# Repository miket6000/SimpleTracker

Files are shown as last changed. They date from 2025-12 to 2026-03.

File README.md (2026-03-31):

# SimpleTracker

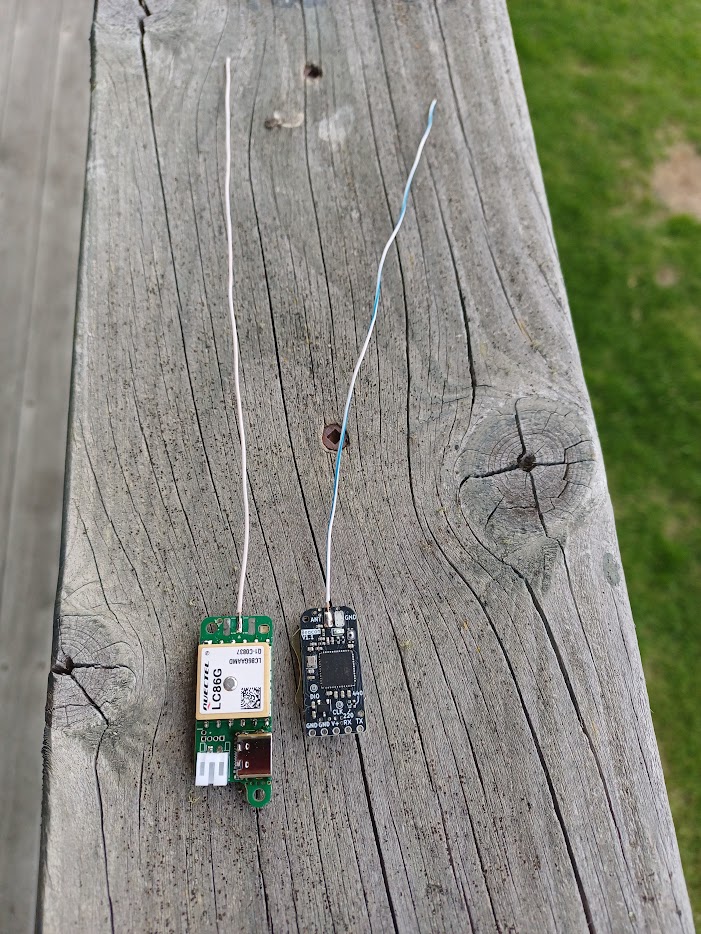
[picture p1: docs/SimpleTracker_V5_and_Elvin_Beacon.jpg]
Photo comparing SimpleTracker to an Elvin Beacon for size Comparison of SimpleTracker \(on the left\) and Elvin Beacon


SimpleTracker is a low cost and easy to use GPS tracker for model rocketry. It can operate of a single 3.7V lipo battery and has a built in charger to enable "plug-&-play" usability. The GPS coordinates of the SimpleTracker are transmitted via 433MHz LoRa every second providing several km of tracking range depending on the antenna used on the SimpleTracker and the ground station. SimpleTracker can also be used as a minimal ground station, reporting the location of a paired tracker via USB serial connection to a PC or phone.

## Hardware

The hardware is fairly minimal. It consist of a battery charger, two 3.3V linear power supplies, a LoRa radio module, GPS and a micro controller with a couple of LEDs to provide status. Bootmode can be enabled by removing the battery and shorting the 'b' and 'v' pins together on the PCB while plugging the tracker into USB. This will put the device into DFU mode so that it can be programmed using dfu-util or STM's programming utilities.

The tracker can be powered by either USB (such as when used as a ground station) or via an AltusMetrum compatible 1s lithium battery. There is an included battery charger that will charge the battery at 100mA if USB is plugged in, so it is recommended that the tracker battery be between 100mAh (to avoid charging it too fast) and 300mAh (to avoid taking too long to charge). Of course there is no upper limit on the capacity of the battery, you can always unplug it to use an external charger if the charge is too slow.

## Firmware
The firmware is "good enough". It can be flashed to the tracker by disconnecting the battery and shorting the "boot" pin to the 3V3 pin right beside it and then plugging in the USB C cable. This will put the tracker into DFU bootloader mode where it can be programmed using CubeIDE or dfu-util.

On power up the module will listen on 434MHz SF 9 BW 125kHz for a command asking for it's UID, or telling it to start transmitting on another channel. Alternatively it can recieve a command via USB if it's acting as a ground station in which case it will issue commands to other trackers. This is all orchestrated by the application.

The LED provides status information via as follows:
 - 1 flash followed by 1 flash - Tracker mode, Waiting for GPS fix
 - 1 flash followed by 2 flashes - Tracker mode, GPS fix is valid
 - 2 flashes followed by 1 flash - Ground station mode, waiting for remote tracker GNSS fix
 - 2 flashes followed by 2 flashes - Ground station mode, remote tracker has GNSS fix
 - 3 flahses - Ground station mode, no remote tracker detected on the current channel in the last 10 seconds

## Application

I decided the application deserved it's own repository, so has been moved to [https://github.com/miket6000/SimpleSuite](https://github.com/miket6000/SimpleSuite). It is built and tested in Linux, with plans on supporting Android.

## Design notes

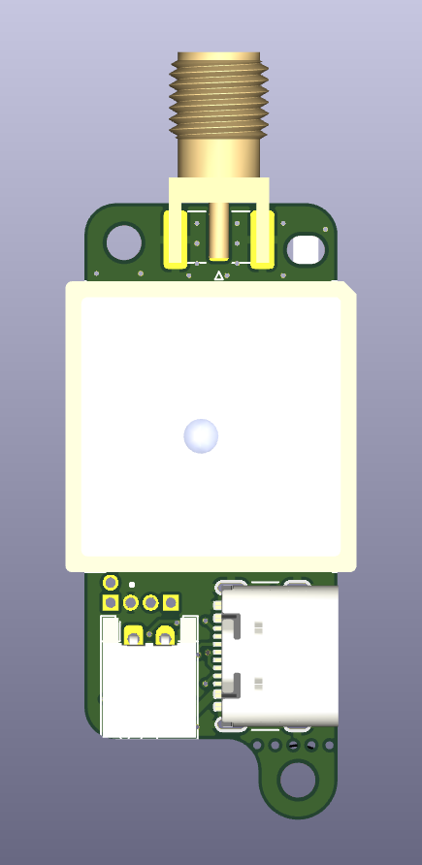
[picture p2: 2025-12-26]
docs/FrontRender.png

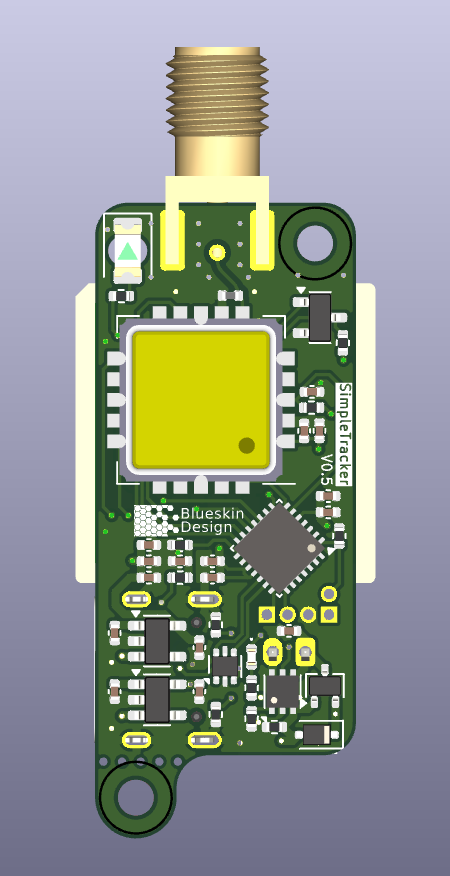
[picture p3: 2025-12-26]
docs/BackRender.png

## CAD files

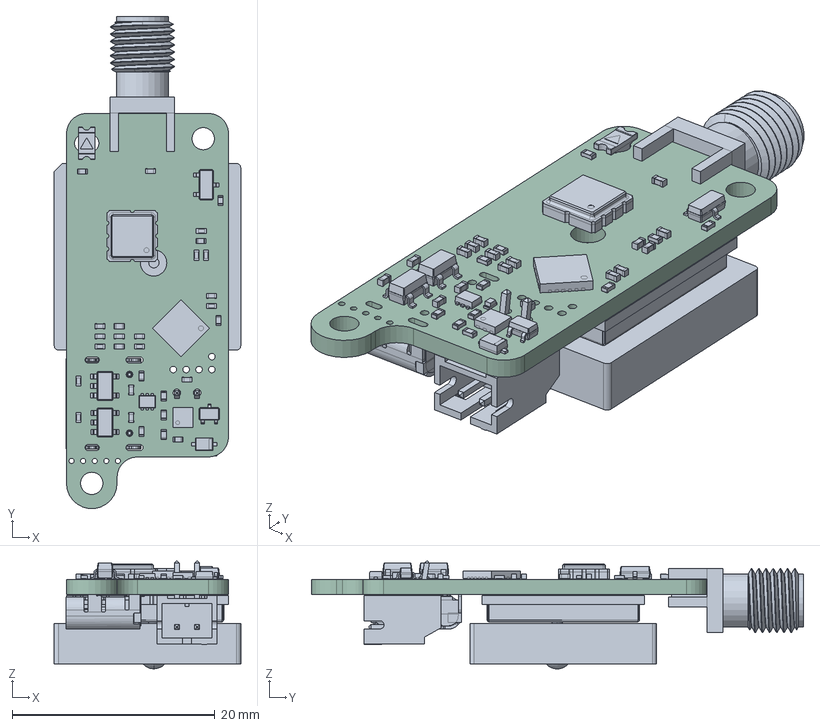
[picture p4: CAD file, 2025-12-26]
hardware/GPS Tracker.step
18.4 x 48.5 x 10.7 mm
SOT-323_SC-70
C_0402_1005Metric x 16
SOT-666
R_0402_1005Metric x 11
LED_1206_3216Metric_Castellated
L_0402_1005Metric
Analog_LCC-8_5x5mm_P1.27mm
LED_0402_1005Metric
D_SOD-323F
SOT-23
DFN-6-1EP_2x2mm_P0.65mm_EP1x1.6mm
SOT-23-5 x 2
QFN-24-1EP_4x4mm_P0.5mm_EP2.7x2.7mm
SMA_Samtec_SMA-J-P-H-ST-EM1_EdgeMount
USB_C_Receptacle_GCT_USB4105-xx-A_16P_TopMnt_Horizontal
LC86G
JST_PH_S2B-PH-K_1x02_P2.00mm_Horizontal
GPS Tracker_PCB

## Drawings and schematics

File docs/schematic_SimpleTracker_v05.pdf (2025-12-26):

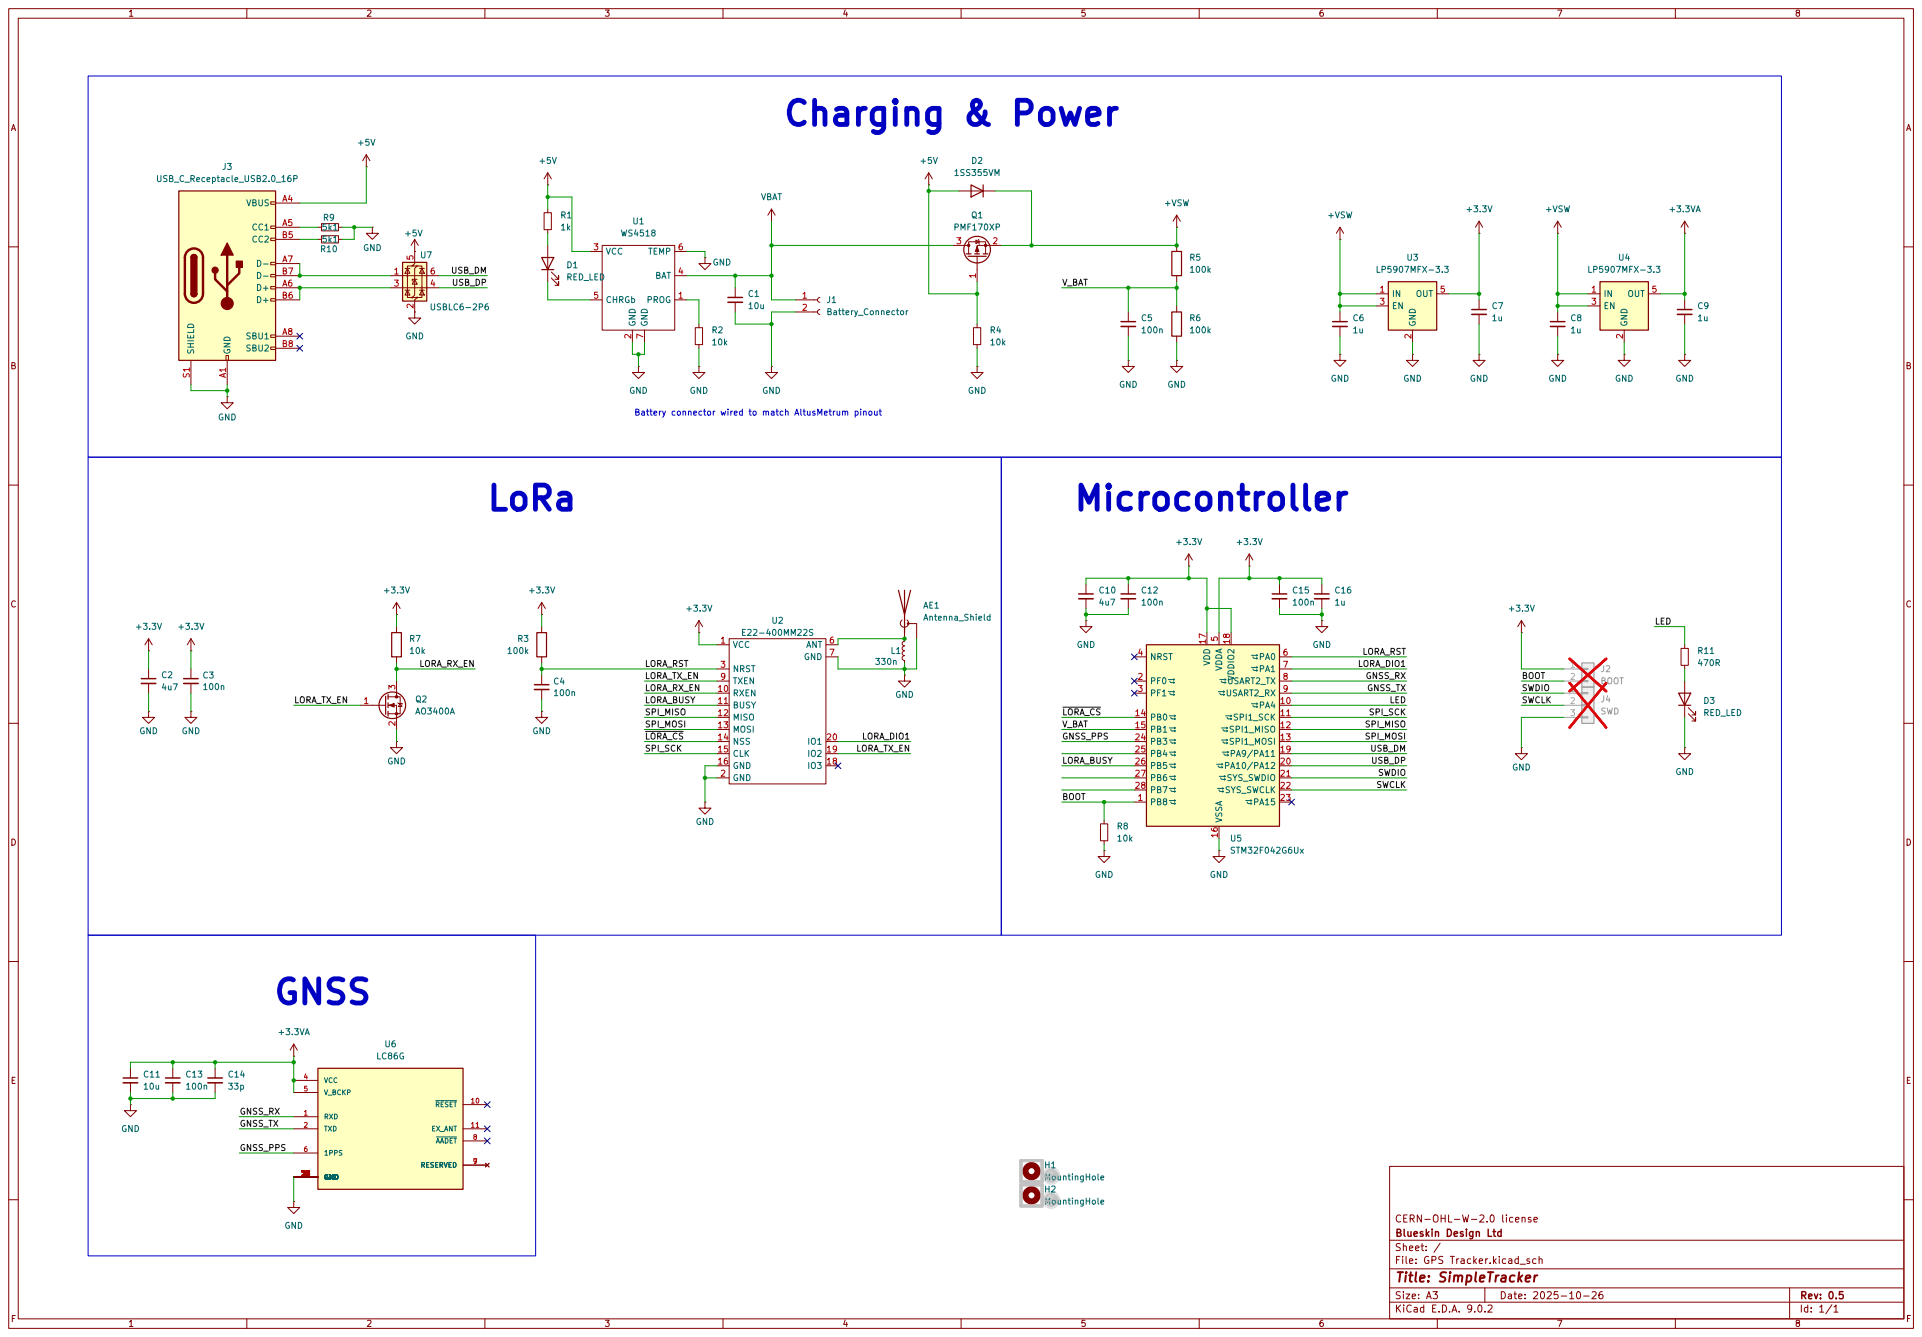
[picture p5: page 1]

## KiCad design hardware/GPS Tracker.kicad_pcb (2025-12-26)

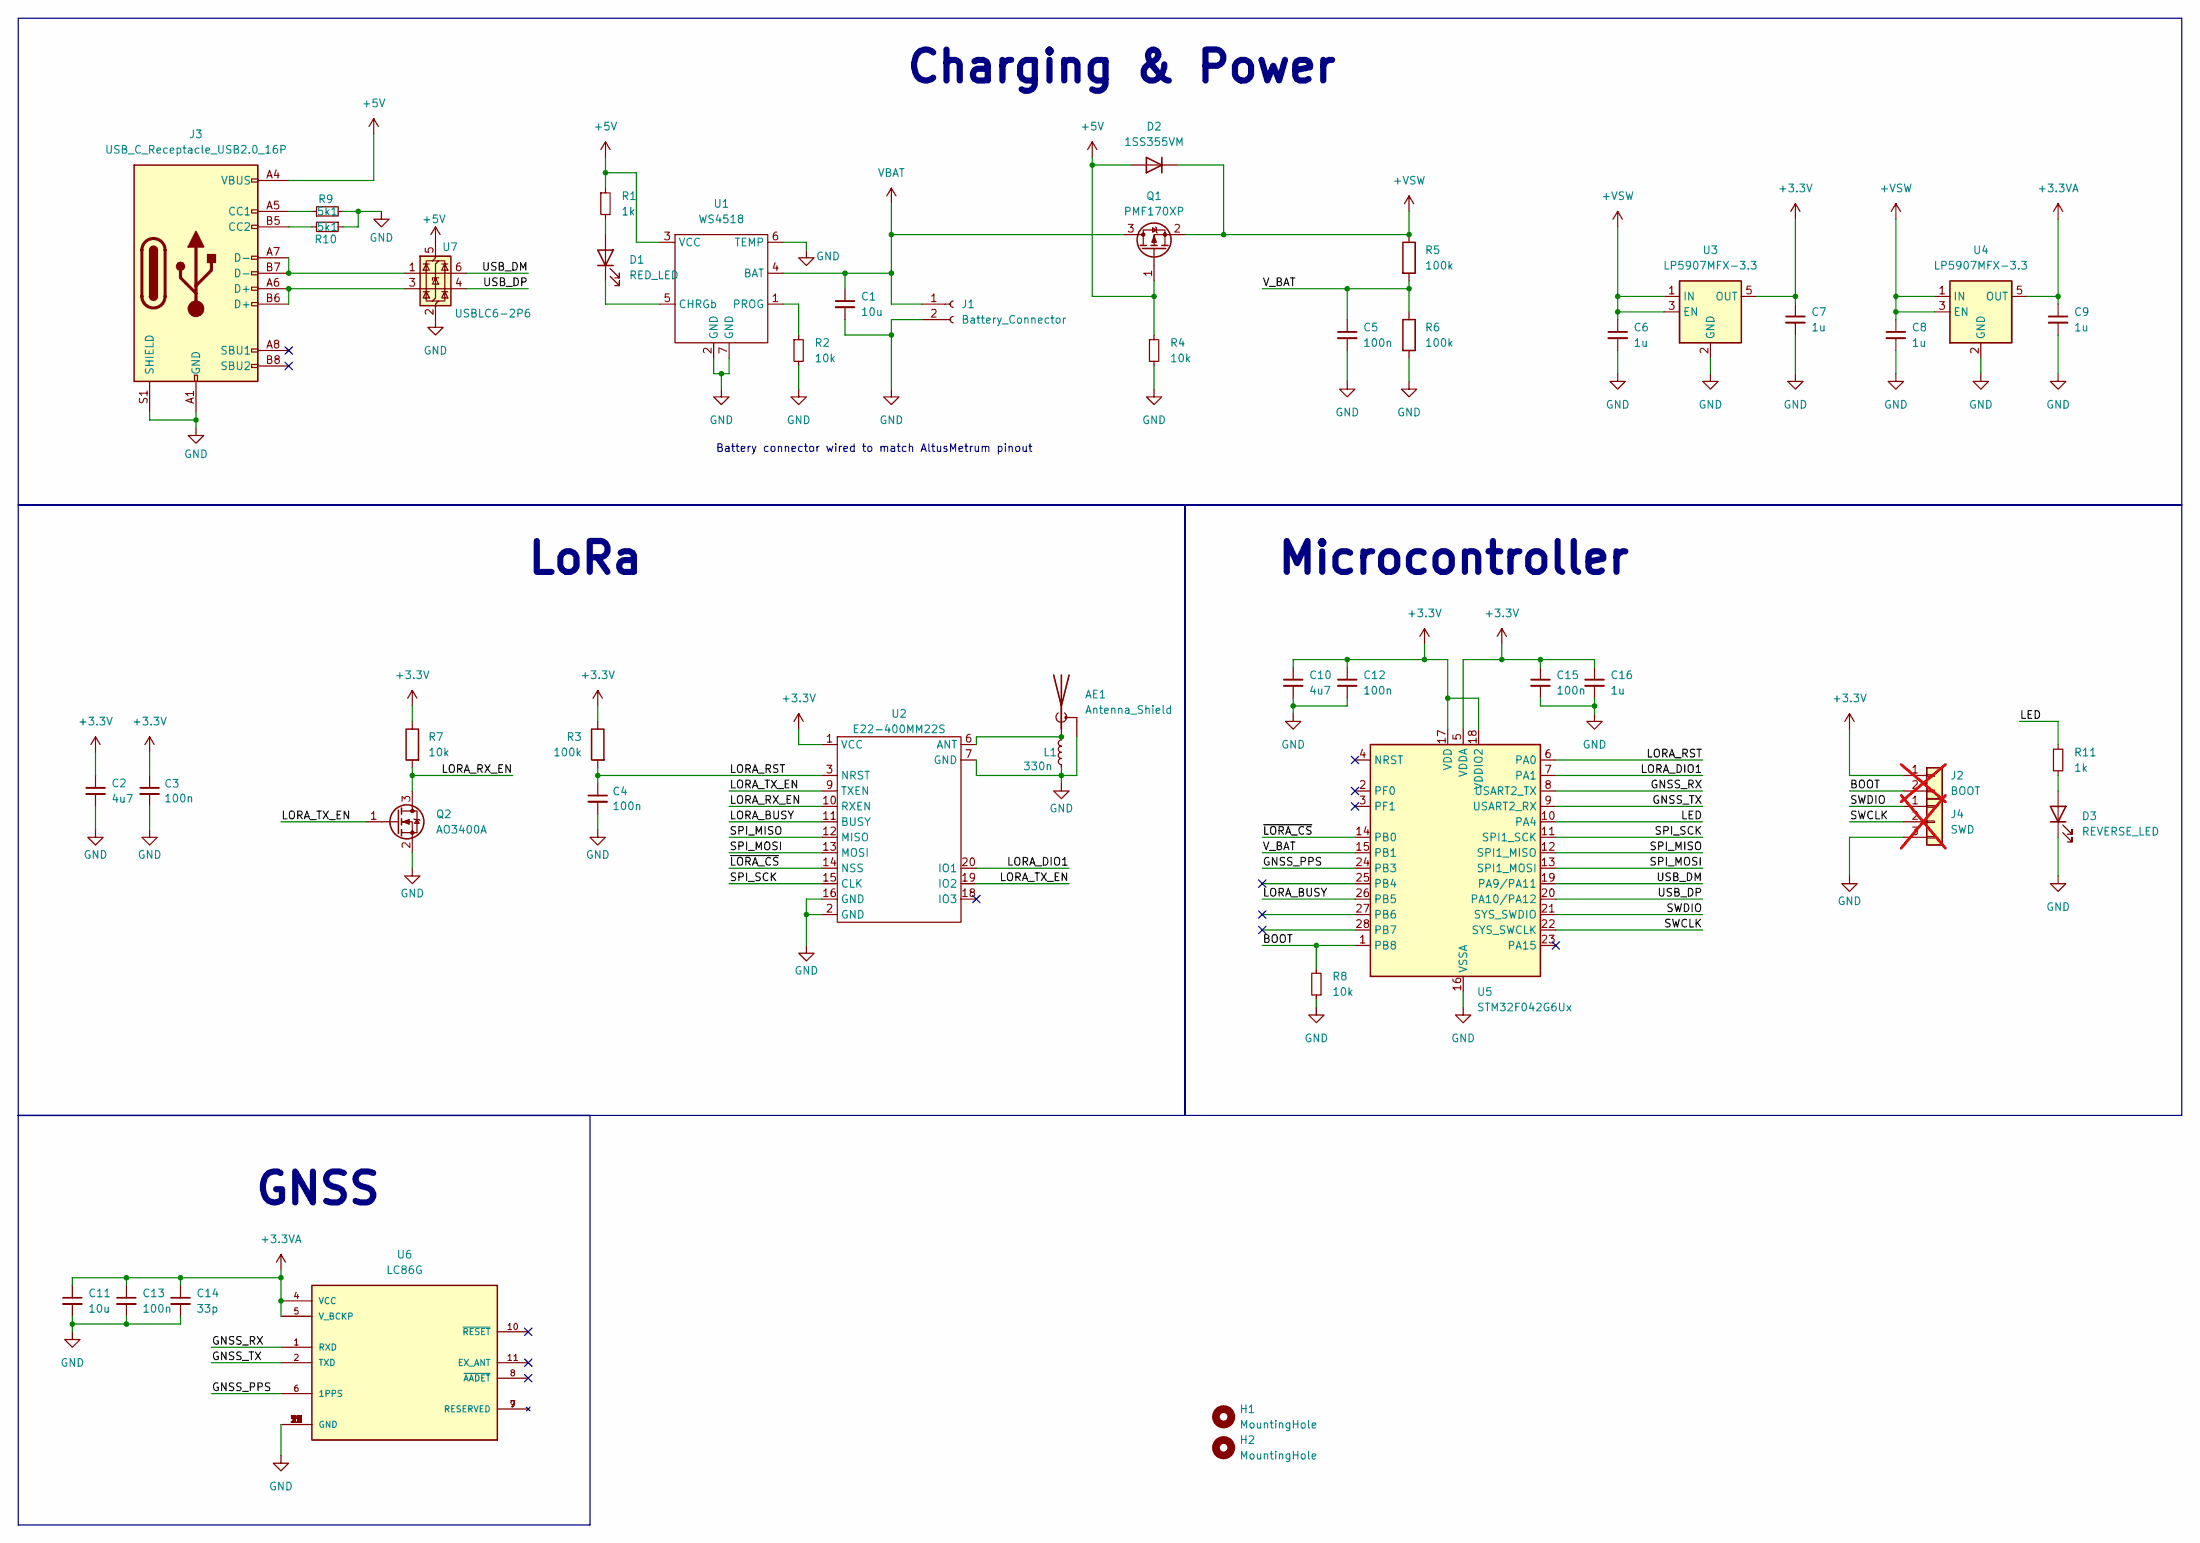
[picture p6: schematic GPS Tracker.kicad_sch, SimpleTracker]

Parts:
AE1: Antenna_Shield; SMA_EdgeMount
C1, C11: 10u; C_0402_1005Metric; JLCPCB Part # C15525
C2, C10: 4u7; C_0402_1005Metric; JLCPCB Part # C23733
C3, C4, C5, C12, C13, C15: 100n; C_0402_1005Metric; JLCPCB Part # C1525
C6, C7, C8, C9, C16: 1u; C_0402_1005Metric; JLCPCB Part # C52923
C14: 33p; C_0402_1005Metric; JLCPCB Part # C1562
D1: RED_LED; LED_0402_1005Metric
D2: 1SS355VM; D_SOD-323F
D3: REVERSE_LED; LED_1206_3216Metric_ReverseMount_Hole1.8x2.4mm; JLCPCB Part # C125107
H1, H2: MountingHole; MountingHole_2.2mm_M2
J1: Battery_Connector; JST_PH_S2B-PH-K_1x02_P2.00mm_Horizontal
J2: BOOT; PinHeader_1x02_P1.27mm_Vertical; not fitted
J3: USB_C_Receptacle_USB2.0_16P; USB_C_Receptacle_GCT_USB4105-xx-A_16P_TopMnt_Horizontal
J4: SWD; PinHeader_1x03_P1.27mm_Vertical; not fitted
L1: 330n; L_0402_1005Metric; JLCPCB Part # C89954
Q1: PMF170XP; SOT-323_SC-70
Q2: AO3400A; SOT-23; JLCPCB Part # C20917
R1, R11: 1k; R_0402_1005Metric; JLCPCB Part # C11702
R2, R4, R7, R8: 10k; R_0402_1005Metric; JLCPCB Part # C25744
R3, R5, R6: 100k; R_0402_1005Metric; JLCPCB Part # C25741
R9, R10: 5k1; R_0402_1005Metric; JLCPCB Part # C25905
U1: WS4518; DFN-6-1EP_2x2mm_P0.65mm_EP1x1.6mm
U2: E22-400MM22S; LCC-20_10x10_Pitch1.27mm
U3, U4: LP5907MFX-3.3; SOT-23-5; JLCPCB Part # C80670
U5: STM32F042G6Ux; QFN-28_4x4mm_P0.5mm
U6: LC86G; XCVR_LC86G_AA
U7: USBLC6-2P6; SOT-666

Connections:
+3.3V: C2.1, C3.1, C7.1, C10.1, C12.1, C15.1, C16.1, J2.1, R3.1, R7.1, U2.1 (VCC), U3.5 (OUT), U5.5 (VDDA), U5.17 (VDD), U5.18 (VDDIO2)
+3.3VA: C9.1, C11.1, C13.1, C14.1, U4.5 (OUT), U6.4 (VCC), U6.5 (V_BCKP)
+5V: D2.2 (A), J3.A4 (VBUS), J3.A9 (VBUS), J3.B4 (VBUS), J3.B9 (VBUS), Q1.1 (G), R1.1, R4.1, U1.3 (VCC), U7.5 (VBUS)
+VSW: C6.1, C8.1, D2.1 (K), Q1.2 (S), R5.1, U3.1 (IN), U3.3 (EN), U4.1 (IN), U4.3 (EN)
/BOOT: J2.2, R8.2, U5.1 (PB8)
/GNSS_PPS: U5.24 (PB3), U6.6 (1PPS)
/GNSS_RX: U5.8 (USART2_TX), U6.1 (RXD)
/GNSS_TX: U5.9 (USART2_RX), U6.2 (TXD)
/LED: R11.1, U5.10 (PA4)
/LORA_BUSY: U2.11 (BUSY), U5.26 (PB5)
/LORA_DIO1: U2.20 (IO1), U5.7 (PA1)
/LORA_RST: C4.1, R3.2, U2.3 (NRST), U5.6 (PA0)
/LORA_RX_EN: Q2.3 (D), R7.2, U2.10 (RXEN)
/LORA_TX_EN: Q2.1 (G), U2.9 (TXEN), U2.19 (IO2)
/SPI_MISO: U2.12 (MISO), U5.12 (SPI1_MISO)
/SPI_MOSI: U2.13 (MOSI), U5.13 (SPI1_MOSI)
/SPI_SCK: U2.15 (CLK), U5.11 (SPI1_SCK)
/SWCLK: J4.2, U5.22 (SYS_SWCLK)
/SWDIO: J4.1, U5.21 (SYS_SWDIO)
/USB_DM: U5.19 (PA9/PA11), U7.6 (I/O1)
/USB_DP: U5.20 (PA10/PA12), U7.4 (I/O2)
/V_BAT: C5.1, R5.2, R6.1, U5.15 (PB1)
/~LORA_CS: U2.14 (NSS), U5.14 (PB0)
GND: AE1.2 (Shield), C1.2, C2.2, C3.2, C4.2, C5.2, C6.2, C7.2, C8.2, C9.2, C10.2, C11.2, C12.2, C13.2, C14.2, C15.2, C16.2, D3.1 (K), J1.2, J3.A1 (GND), J3.A12 (GND), J3.B1 (GND), J3.B12 (GND), J3.S1 (SHIELD), J4.3, L1.2, Q2.2 (S), R2.2, R4.2, R6.2, R8.1, R9.2, R10.1, U1.2 (GND), U1.6 (TEMP), U1.7 (GND), U2.2 (GND), U2.7 (GND), U2.16 (GND), U3.2 (GND), U4.2 (GND), U5.16 (VSSA), U6.3 (GND), U6.12 (GND), U6.13 (GND), U6.14 (GND), U6.15 (GND), U6.16 (GND), U6.17 (GND), U6.18 (GND), U6.19 (GND), U6.20 (GND), U6.21 (GND), U6.22 (GND), U6.23 (GND), U6.24 (GND), U6.25 (GND), U6.26 (GND), U6.27 (GND), U6.28 (GND), U6.29 (GND), U6.30 (GND), U6.31 (GND), U6.32 (GND), U6.33 (GND), U6.34 (GND), U6.35 (GND), U6.36 (GND), U7.2 (GND)
unnamed: AE1.1 (A), L1.1, U2.6 (ANT)
unnamed: D1.2 (A), R1.2
unnamed: D1.1 (K), U1.5 (CHRGb)
unnamed: D3.2 (A), R11.2
unnamed: J3.A5 (CC1), R9.1
unnamed: J3.B5 (CC2), R10.2
unnamed: J3.A6 (D+), J3.B6 (D+), U7.3 (I/O2)
unnamed: J3.A7 (D-), J3.B7 (D-), U7.1 (I/O1)
unnamed: R2.1, U1.1 (PROG)
VBAT: C1.1, J1.1, Q1.3 (D), U1.4 (BAT)

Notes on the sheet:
Charging & Power
GNSS
Battery connector wired to match AltusMetrum pinout
Microcontroller
LoRa

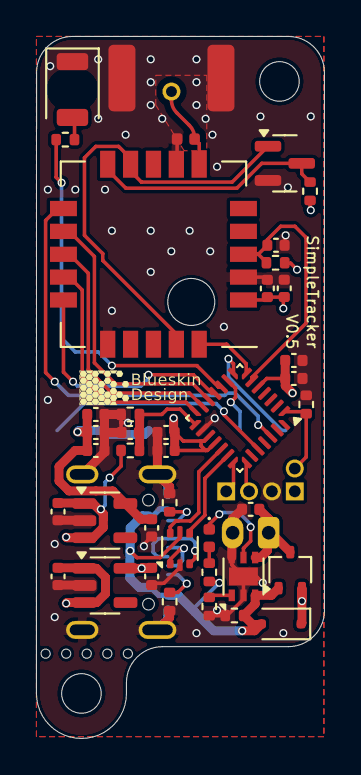
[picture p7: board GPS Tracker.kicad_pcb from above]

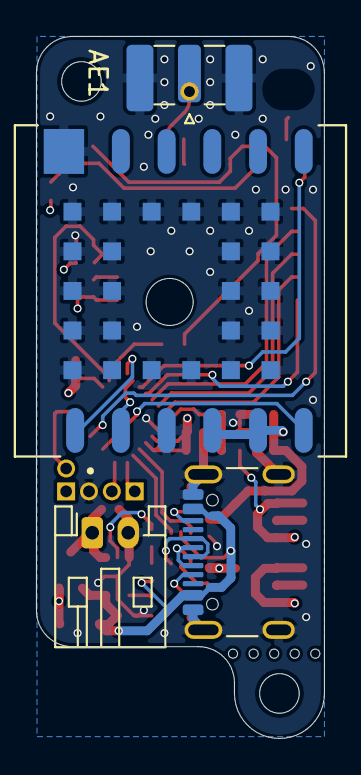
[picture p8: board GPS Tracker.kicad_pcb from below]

Board: 4 copper layers, 16.0 x 39.0 mm, 47 parts (6 on the bottom side), 34 nets.

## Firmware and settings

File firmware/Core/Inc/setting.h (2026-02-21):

#ifndef SETTING_H
#define SETTING_H
#include "main.h"
#include "lora.h"
#include "app_context.h"

#define MAX_SETTING_LIST_SIZE 10

#define DEFAULT_FREQ      434000000UL
#define DEFAULT_SF        LORA_SF9
#define DEFAULT_BW        LORA_BW_125
#define DEFAULT_CR        LORA_CR_4_5
#define DEFAULT_POWER     LORA_TX_POWER_22_DBM
#define DEFAULT_OC        150
#define DEFAULT_PREAMBLE  8
#define DEFAULT_MODE      MODE_TRACKER

typedef struct {
  char label;
  uint32_t value;
  uint32_t initial;
} Setting;

Setting **get_settings();
void setting_reset();
Setting *setting(char label);

#endif // SETTING_H

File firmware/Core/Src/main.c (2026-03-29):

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
/* Includes ------------------------------------------------------------------*/
#include "main.h"
#include "spi.h"
#include "tim.h"
#include "usart.h"
#include "gpio.h"
#include "adc.h"

/* USER CODE BEGIN Includes */
#include "clock.h"
#include "board.h"
#include "usb.h"
#include "usbd_conf.h"
#include "usbd_core.h"
#include "led.h"
#include "led_sequences.h"
#include "app_context.h"
#include "task.h"
#include "tasks.h"
#include "setting.h"
#include "filesystem.h"
#include "command.h"
#include "commands.h"
#include "gps.h"
#include "lora.h"
#include "lora_arbitration.h"
#include "lora_discovery.h"
#include "event.h"
#include "config.h"
#include <stdbool.h>
#include <stdlib.h>
#include "tusb.h"
#include "uid.h"

/* USER CODE END Includes */


/* USER CODE BEGIN PV */
LedHandle status_led;
LoRa_t hlora;

AppContext_t appContext = {
  .gpsFix = false, 
  .led = &status_led, 
  .lora = &hlora,
  .mode = MODE_GROUND_STATION,
};

/* USER CODE END PV */

/* USER CODE BEGIN 0 */

void load_settings() {
  uint8_t i = 0;
  Setting **settingList = get_settings();
  while (settingList[i] != NULL) {
    fs_read_config(settingList[i]->label, &settingList[i]->value);
    i++;
  }
}

void lora_init(LoRa_t *hlora) {
  
  hlora->frequency = setting('f')->value;
  hlora->spreadingFactor = setting('s')->value;
  hlora->bandwidth = setting('b')->value;
  hlora->codingRate = setting('c')->value;
  hlora->txPower = setting('d')->value;
  hlora->preambleLength = setting('p')->value;
  hlora->crcEnabled = 0;

  hlora->nss_port = LORA_CS_GPIO_Port;
  hlora->nss_pin = LORA_CS_Pin;
  hlora->busy_port = LORA_BUSY_GPIO_Port;
  hlora->busy_pin = LORA_BUSY_Pin;
  hlora->reset_port = LORA_RST_GPIO_Port;
  hlora->reset_pin = LORA_RST_Pin;
  hlora->dio1_port = LORA_DIO1_GPIO_Port;
  hlora->dio1_pin = LORA_DIO1_Pin;
  hlora->hspi = &hspi1;

  LoRa_Init(hlora);
}

void HAL_GPIO_EXTI_Callback(uint16_t GPIO_Pin)
{
    if (GPIO_Pin == LORA_DIO1_Pin)
    {
        LoRa_IrqHandler(appContext.lora);
    }
}

/* USER CODE END 0 */

/**
 * @brief  The application entry point.
 * @retval int
 */
int main(void) {

  /* MCU Configuration--------------------------------------------------------*/

  /* Reset of all peripherals, Initializes the Flash interface and the Systick. */
  HAL_Init();

  /* Configure the system clock */
  SystemClock_Config();

  /* Initialize all configured peripherals */
  MX_GPIO_Init();
  MX_SPI1_Init();
  MX_USB_PCD_Init();
  MX_USART2_UART_Init();
  MX_TIM16_Init();
  MX_ADC_Init();
  /* USER CODE BEGIN 2 */

  //led(&status_led, LED_ON);
  /* Initialize flash filesystem and load settings */
  fs_init();
  load_settings();
  led_init(&status_led, LED_GPIO_Port, LED_Pin);
  led_add_sequence(&status_led, idle_sequence);
  tusb_init();

  /* populate appContext with values that are now available */
  //appContext.mode = setting('m')->value;

  //appContext.mode = MODE_TRACKER;
  appContext.mode = MODE_GROUND_STATION;
  appContext.uid = UID_Get();
  strncpy(appContext.uidStr, UID_GetString(), 8);
  appContext.uidStr[8] = '\0';

  /* Seed the PRNG for LoRa collision avoidance with device UID */
  lora_seed_prng(appContext.uid);
  
  /* init command line interpreter */
  cmd_add("REBOOT", reboot, NULL);
  cmd_add("I", cmd_set_interactive, NULL);
  cmd_add("i", cmd_unset_interactive, NULL);
  cmd_add("R", print_remote, &appContext);
  cmd_add("L", print_str_ptr, &appContext.lastGpsSentence);
  cmd_add("T", transmit, &appContext);
  cmd_add("SCAN", scan, &appContext);
  cmd_add("PAIR", pair, &appContext);
  cmd_add("SET", set_config, NULL);
  cmd_add("GET", get_config, NULL);
  cmd_add("UID", print_str, &appContext.uidStr);
  cmd_add("D", discovery_read, &appContext);
  cmd_add("C", channel_switch, &appContext);
  //cmd_add("ERASE", erase_flash, NULL); 
  cmd_add("FACTORY", factory_reset, NULL);
  cmd_set_print_function(print); 

  /* Architecture description.
   * 
   * Low level drivers are primarily handled by a task scheduler. This includes polling 
   * the LoRa module, flashing LEDs and managing the USB Tx and Rx buffers. These task 
   * must happen in a timely manner for the operation of the tracker.
   *
   * Some task are interrupt driven, most notably the GPS receiver / parser and LoRa 
   * event completion.
   *
   * Higher level logic is taken care of using an event driven framework. For example,
   * the GPS rx interrupt will generate an event if it detects a valid GNGGA packet,
   * which then potentially creates a lora_tx event. 
   *
   */

  /* init lora & gps modules */
  //HAL_Delay(3000); // short delay to allow user to view init over serial.
  lora_init(&hlora);
  gps_init(&huart2);

  /* create task, arguments are init_delay, period, callback, parameter */
  task_build(0, 100, task_led, &appContext);
  task_build(0, 100, task_lora, &appContext);
  task_build(0, 0, task_usb, &appContext);
  task_build(0, 2500, task_measure_voltage, &appContext);
  task_build(0, 10, task_gps, &appContext);
  task_build(0, 0, lora_process_delayed_response, &appContext);
  
  // Rx needs to be started once, will restart itself
  LoRa_Receive(&hlora, LORA_RX_TIMEOUT_MS);

  /* USER CODE END 2 */

  /* Infinite loop */
  /* USER CODE BEGIN WHILE */
  while (1)
  {
    /* USER CODE END WHILE */

    /* USER CODE BEGIN 3 */

    // Time dependant task
    task_run();
    eventDispatcher(&appContext);
    //power_management();
  }

  /* USER CODE END 3 */
}

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


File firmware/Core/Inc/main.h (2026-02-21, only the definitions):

#define LORA_RST_Pin GPIO_PIN_0
#define LORA_RST_GPIO_Port GPIOA
#define LORA_DIO1_Pin GPIO_PIN_1
#define LORA_DIO1_GPIO_Port GPIOA
#define LORA_CS_Pin GPIO_PIN_0
#define LORA_CS_GPIO_Port GPIOB
#define LORA_BUSY_Pin GPIO_PIN_5
#define LORA_BUSY_GPIO_Port GPIOB
#define GNSS_PPS_Pin GPIO_PIN_3
#define GNSS_PPS_GPIO_Port GPIOB
#define LED_Pin GPIO_PIN_4
#define LED_GPIO_Port GPIOA
#define VOLTAGE_Pin GPIO_PIN_1
#define VOLTAGE_GPIO_Port GPIOB

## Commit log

2025-01-07 Initial commit with hardware, mostly working firmware, and a basic python app with receiver based diversity.
    [GPS Tracker.kicad_pcb, GPS Tracker.kicad_sch]
2025-03-15 added error handling to the serial comms to provide more graceful handling of non-printable characters.
2025-03-15 added additional settings, and cleaned up lora library to avoid pulling in double library
    [lora.c, main.c, setting.h]
2025-03-16 fixed commands to allow automated reporting to be turned on and off, and to allow reading out of local GPS coordinate from receiver.
    [main.c]
2025-04-13 updated documentation by adding BoM, image and schematic pdf.
    [bom.csv]
2025-07-21 copied across architectural improvements from V2 hardware. Now using a simplified task and event driven framework
    [GPS Tracker.kicad_pcb, GPS Tracker.step]
2025-09-25 Hard replaced with v0.2 hardware & firmware and removed app (now in it's own repository)
    [GPS Tracker.kicad_pcb, GPS Tracker.kicad_sch, GPS Tracker.step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]
2025-09-25 Added hardware for v0.3 removed firmware as new micro controller
    [GPS Tracker.kicad_pcb, GPS Tracker.kicad_sch, GPS Tracker.step]
2025-09-28 Changed pinout on nRF52 to move SPI to full speed pins. This required a total re-layout.
    [GPS Tracker.kicad_pcb, GPS Tracker.kicad_sch]
2025-10-01 Corrected lora module TXEN/RXEN so that it can be automatically controlled by DIO2, no longer requiring the micro pins. Also connected DIO1 to the micro to make the hardware compatible with the Zephy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
    [GPS Tracker.kicad_pcb, GPS Tracker.kicad_sch]
2025-10-13 Cleaned up routing slightly and changed programming connector to 2x3 to match tag connect pinout.
    [GPS Tracker.kicad_pcb, GPS Tracker.kicad_sch]
2025-10-13 updated pdf schematic to match kicad schematic
2025-10-22 New alternative option similar to V0.1 except with updated GPS and LoRa Modules, improved power path circuitry, rotated USB socket and a propper power connector.
    [GPS Tracker.kicad_pcb, GPS Tracker.kicad_sch]
2025-10-26 Updated board to reduce width by 2mm (now 16mmx38mm bounding rectangle), added USB ESD protection, and cleaned up schematic.
    [GPS Tracker.kicad_pcb, GPS Tracker.kicad_sch, GPS Tracker.step]
2025-12-26 Updated documentation and schematics to reflect latest revision
    [GPS Tracker.kicad_pcb, GPS Tracker.kicad_sch, GPS Tracker.step]
2025-12-26 improved LED flashing patterns and corrected version control error in event_gps.
    [main.c]
2026-02-10 Total rewrite of LoRa code and API, minor updates to printing and other functionality.
2026-02-12 Fixed clock stability issue during startup, added factory reset command, fixed LoRa default settings to work within modules clock stability capability.
    [clock.c, lora.c, main.c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]
2026-02-21 Major changes to mode control. Now initialize as a ground station until receiving a lora command telling the tracker that it is a tracker. This was to prevent transmitting during charging. Also added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
    [lora.c]
2026-02-22 rewrite of GPS to use steaming of bytes and a task to create events when the correct sentence is received.
    [gps.c]
2026-03-14 Fixed bug in transition to paired mode for ground station.
    [lora.c, main.c]
2026-03-28 Upgraded LED library to a more flexible sequence engine and changed GPS on-air format to binary to reduce transmission duration. This required a NMEA packer/unpacker to maintain compatibility with th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
2026-03-29 minor tidy up of code, main fix was dealing nicely with small UIDs by prepending leading zeros.
    [led.c, main.c]

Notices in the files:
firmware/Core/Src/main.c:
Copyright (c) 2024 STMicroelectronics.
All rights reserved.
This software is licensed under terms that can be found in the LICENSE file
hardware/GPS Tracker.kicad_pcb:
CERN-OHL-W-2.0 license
